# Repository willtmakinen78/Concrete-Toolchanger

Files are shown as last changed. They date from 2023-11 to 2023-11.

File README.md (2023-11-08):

# Concrete-Toolchanger
My senior thesis project from Princeton consisted of developing a multi-material concrete 3D-printer.

Using an E3D TOolchanger as the base motion system, custom concrete and silicone extruders were developed to be compatible with the toolchanging system.
A system for reliably priming the polymer Hemera extruders was also developed. The mechanics and electronics were controlled using a Duet board and RRF3,
which allowed for all of the toolchanging procedures and material interactions to be controlled by macros. Additionally, rather than using a traditional
slicer, FullControlGCode was used to create parametric toolpaths tailored to each type of extruder. Together, silicone and polymers were combined with
cement and mortar to create new concrete multi-materials with augmented material properties.

Check out the full thesis PDF for more details!

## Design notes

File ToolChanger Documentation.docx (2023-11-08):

ToolChanger Documentation

Introduction

Rather than being a full step-by-step guide, this document is mainly designed to serve as a collection of information sources with brief explanations in between. The other information sources linked here explain the various parts of the system well and in more detail than could be provided here, so they should be the primary resources for troubleshooting with this document only filling in the gaps.

Connecting to the ToolChanger

The printer can be accessed in two ways, over USB (https://learn.ooznest.co.uk/Guide/1.+Connecting+your+Duet+via+USB+-+Windows/123) and via the Duet Web Control (https://duet3d.dozuki.com/c/DuetWebControl) interface. The USB interface is minimal, and should only be used when first connecting the Duet control board (the Duet 2 Ethernet (https://docs.duet3d.com/Duet3D_hardware/Duet_2_family/Duet_2_WiFi_Ethernet_Hardware_Overview) is currently being used) to a network. The Duet board was configured over USB to use the static IP address (https://docs.duet3d.com/Duet3D_hardware/Duet_2_family/Duet_2_WiFi_Ethernet_Hardware_Overview) of 192.168.2.1. Then, the ethernet cable was plugged directly into an ethernet port of the control computer, and configured as is described here (https://duet3d.dozuki.com/Wiki/Setting_up_networking_on_Duet#Section_Wired_direct_connection). With this, the Duet Web Control interface can be accessed by going to 192.168.2.1 in a web browser.

Using Duet Web Control

An overview of the various functions of Duet Web Control is available here (https://duet3d.dozuki.com/Wiki/Duet_Web_Control_v2_and_v3_%28DWC%29_Manual). The most important aspects of it specific to the ToolChanger are the macro files (https://duet3d.dozuki.com/Wiki/Setting_up_macro_files_for_common_tasks) accessible from the Macros tab and system .g gcode files accessible from the System tab. The macro file do not have a file extension and can only be run from the Marcos or Dashboard tabs. The gcode files in the System tab have the .g file extension and can be run from anywhere using the M98 (https://duet3d.dozuki.com/Wiki/M98) command. This can be from the built-in console, within toolpath gcode files, or even from within other system .g files.

The most important system file is config.g. This is run at system startup and whenever the printer is reset, and sets the configuration of toolheads, heaters, offsets, and more. Looking through it, most of the lines are commented describing what is being configured, and each M command can be googled to get more information on what they are doing. Most relevant to the work being done this summer is lines 127-136 configuring the toolhead offsets. These will need to be modified if the geometry of any of the toolheads are changed, putting their nozzles in different locations.

There are also various system .g files used internally by the firmware of the printer, as described here (https://duet3d.dozuki.com/Wiki/ConfiguringRepRapFirmwareCartesianPrinter). These are used during various actions such as pausing, resuming, and stopping a print. The files that will most likely need to be changed are the tpre[tool number], tpost[tool number] and tfree[tool number]. These are called before and after a tool is selected (tpre and tpost) using the command T[toolnum] and when a tool is dropped off using T-1 (or when directly switching from one tool to another, e.g. if T0 is selected, sending the command T2 will actually execute T-1 and then T2. So the sequence of .g files called will be tfree0.g, tpre2.g, tpost2.g.). Opening up and reading these files, the tool pickup and drop-off locations in the tpre and tfree files will have to be changed if the tool geometries are changed, as well as the Z safety distances denoted by the WARNING comments. This is all described in more detail here (https://duet3d.dozuki.com/Wiki/Multiple_tools_and_Tool_change_macros#Section_Tool_Change_Macros).

Printer configuration

Currently, there are two plastic Hemera (https://e3d-online.com/products/e3d-hemera-direct-kit-1-75mm) tools, one syringe-based tool, and one hardware store silicone tube-based tool installed on the ToolChanger. The hemera tools both have 1.2mm nozzles installed, however smaller nozzles are on hand in the cardboard parts bin in the corner of the work bench. Additionally, two other complete hemera kits are also on hand, if one wishes to switch out the other two tools for additional plastic extruders.

From left to right, the tools are T0, T1, T2, and T3 which are hemera, hemera, syringe, and silicone tube extruders.

If a tool geometry were to be changed, it would have to be able to accept a tool plate (the metal part) and the plastic tool receptable (black plastic) in order for the kinematic coupling mechanism to be able to interface with it and for it to be able to be parked to the machine frame. The ToolChanger Github is available here (https://github.com/e3donline/ToolChanger) with PDFs and the original CAD parts.

Gcode/Toolpath Generation

The ToolChanger runs on RepRapFirmware3 (https://duet3d.dozuki.com/Wiki/RepRapFirmware_3_overview) (RRF3). Here (https://duet3d.dozuki.com/Wiki/Gcode) is its gcode dictionary. A notable feature is its scripting abilities (https://duet3d.dozuki.com/Wiki/GCode_Meta_Commands), which can be very powerful. Gcodes can be generated using slicers, grasshopper, or the excel-based FullControl Gcode (https://fullcontrolgcode.com/). FullControl was used extensively this past year to decent results. Example designs can be found in the FullControl folder in the IP Accelerator Dropbox. Note that if a different designer is used, the starting and ending gcodes from the FullControl designs should be copied over to ensure proper starting and ending of prints.

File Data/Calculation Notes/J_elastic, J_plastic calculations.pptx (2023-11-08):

## J_elastic, J_plastic calculations

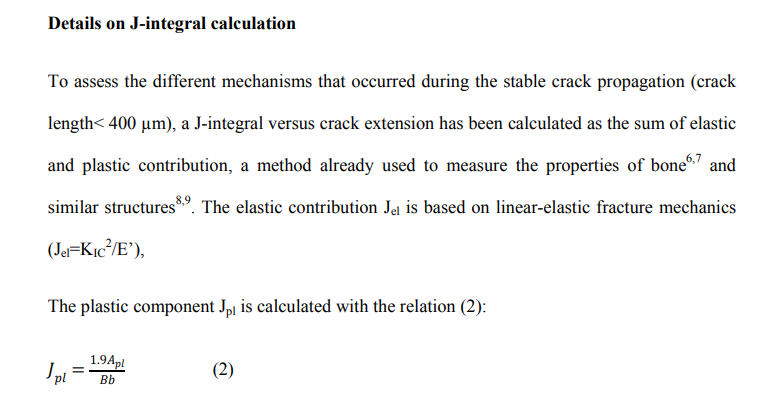
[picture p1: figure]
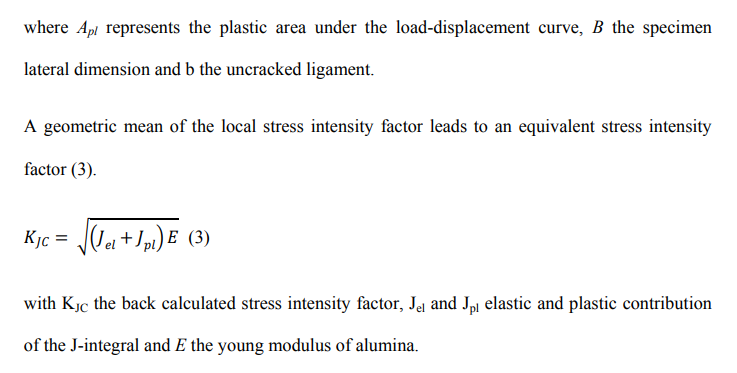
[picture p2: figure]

## J_elastic, J_plastic calculations

Term Definitions:
K = stress intensity factor is used to predict the stress state near the tip of a crack due to remote/residual stresses
Kc = critical stress intensity factor is the stress at which unstable crack propagation occurs
G = energy release rate, ie. rate at which energy is transformed as a material undergoes fracture
J = integral used to calculate the strain energy release rate per unit of fracture surface area
R-curve = quantification of the principle of increasing fracture resistance, as a function of crack length

## J_elastic, J_plastic calculations

Following E1820:
For basic test method using a notched 3PB test,
Where J_plastic is defined as:

## J_elastic, J_plastic calculations

For calculating J_elastic, we first need K:

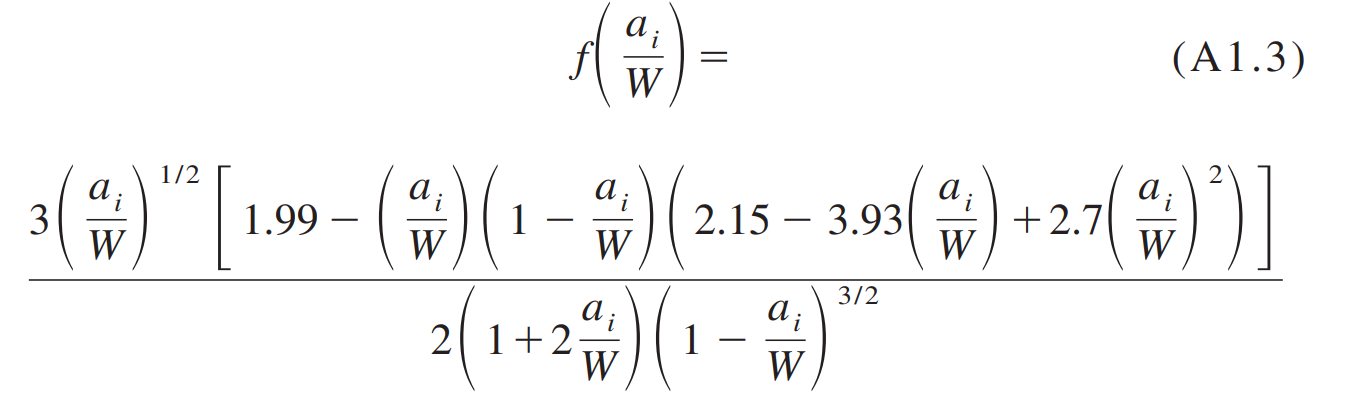
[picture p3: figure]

## J_elastic, J_plastic calculations

- P_i = force applied (N)
- S = span length (m)
- B = specimen thickness (m)
- B_N = specimen thickness between roots of the side grooves (m) – equivalent to B for our test (E399-20a 8.2.1)
- a_i = crack size (m)
- W = specimen depth (m)

## J_elastic, J_plastic calculations

Crack size, a_i, is calculated based on the CMOD measurements shown in the formulas in E399:

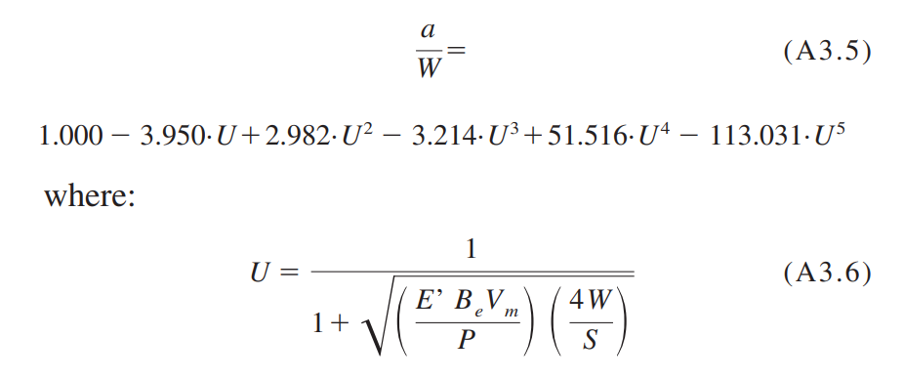
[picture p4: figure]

## J_elastic, J_plastic calculations

For J_plastic, we need the following terms:
…And alpha_0 = initial crack length

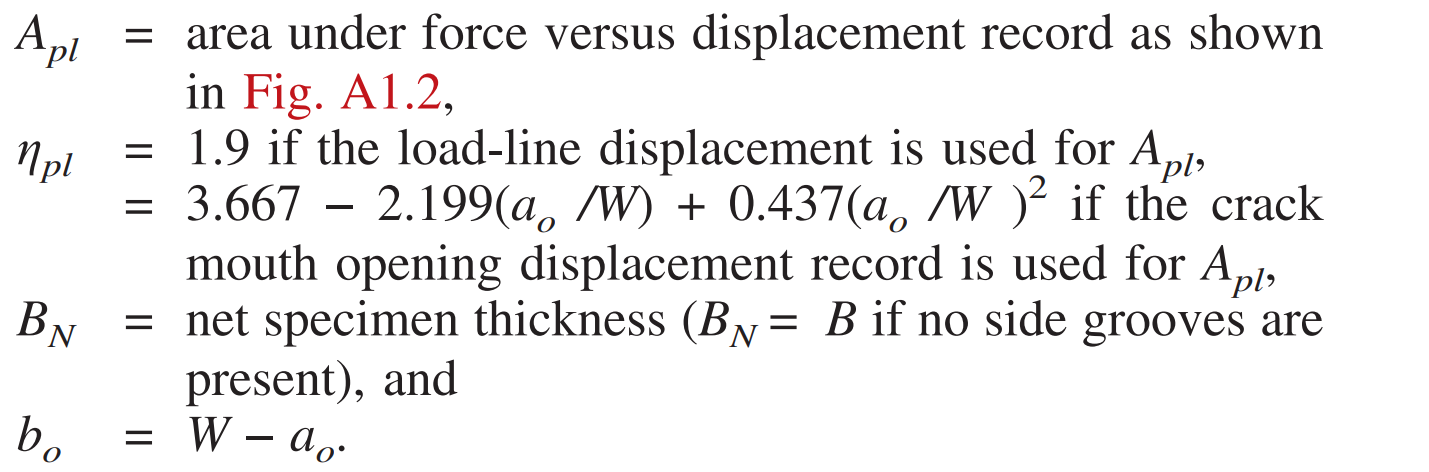
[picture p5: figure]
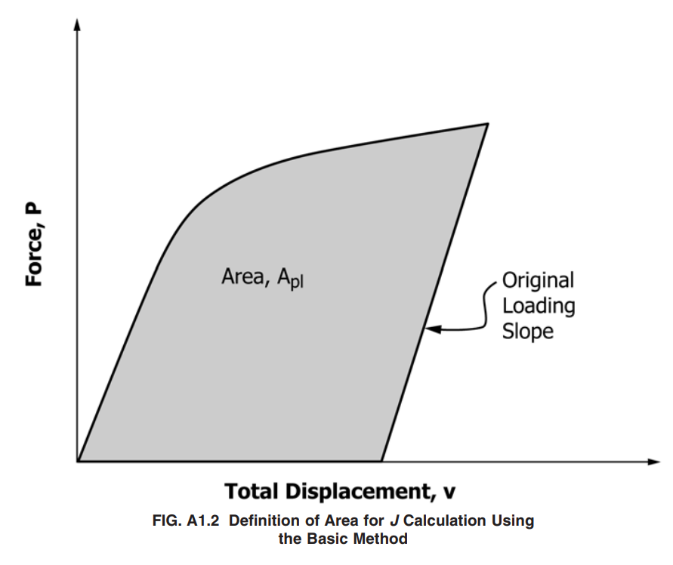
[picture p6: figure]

## J_elastic, J_plastic calculations

We can then solve for the final J value:
A correction factor is applied to the final J-integral

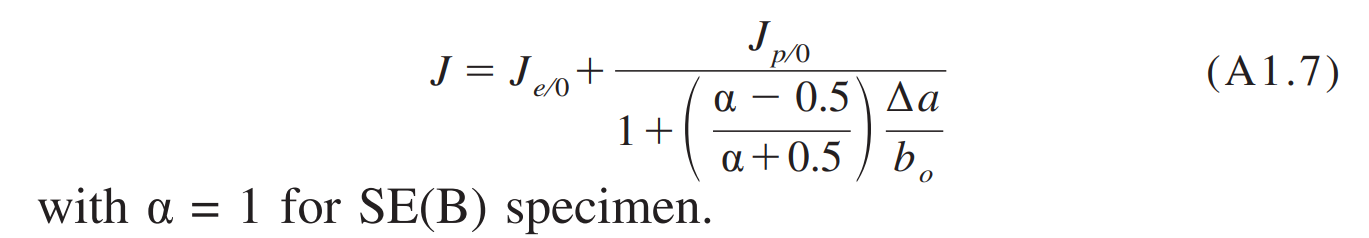
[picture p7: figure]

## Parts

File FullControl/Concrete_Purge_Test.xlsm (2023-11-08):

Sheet: Main Sheet
 |  |  |  |  |  |  |  | ;GCODE generated with FullControl GCODE Designer software - contact Andy Gleadall (a.gleadall@lboro.ac.uk) for more information
 |  |  |  |  |  |  |  |  |  |  |  |  |  | Recycle bin designs: | 1
Design ID: | Interlaced_Lines | Save to sheet: | MyDesigns
Feature |  |  |  |  |  |  |  |  |  |  |  | Comments
1 | Line | Cartesian | 227 | 163.6 | 0 | R-125 | R0 | R0 | Print | 1.6002 | 1.8 |  | Settings
2 | Line | Cartesian | R0 | R0 | R0 | R0 | R-2 | R0 | Print | 1.6002 | 1.8 |  | Zoffset | 1.3 | mm
3 | Line | Cartesian | R0 | R0 | R0 | R125 | R0 | R0 | Print | 1.6002 | 1.8 |  | FirstLayerExtrusionMultiplier | 1 | no units
4 | Line | Cartesian | R0 | R0 | R0 | R0 | R-4.7 | R0 | Print | 1.6002 | 1.8 |  | FirstLayerNozzleSpeedMultiplier | 1 | no units
5 | Cartesian repeat | 1-4 | 0 | -6.7 | 0 | 5 |  |  |  |  |  |  | ToolChange ID | Default |  | Default | Default | Default | Default | Default | Default | Raise3D_2nozzle | Tool changer | Default | Default | Default | Default | Default
6 | Retraction | 0 | 0 | 1.3 | 10000 |  |  |  |  |  |  |  | Start tool (after StartGCODE) | 0
7 | Line | Cartesian | R0 | R0 | R0 | R0 | R4.7 | R0 | Print | 1.6002 | 1.8
8 | Line | Cartesian | R0 | R0 | R0 | R-125 | R0 | R0 | Print | 1.6002 | 1.8 |  | BedTemp | 0 | C | 60 | 60 | 60 | 60 | 60 | 60 | 60 | 60 | 60 | 60 | 60 | 60 | 60
9 | Line | Cartesian | R0 | R0 | R0 | R0 | R2 | R0 | Print | 1.6002 | 1.8 |  | NozzleFeedratePrinting | 600 | mm/min
10 | Line | Cartesian | R0 | R0 | R0 | R125 | R0 | R0 | Print | 1.6002 | 1.8 |  | NozzleFeedrateTravelling | 3000 | mm/min
11 | Cartesian repeat | 7-10 | 0 | 6.7 | 0 | 5 |  |  |  |  |  |  | NozzleTemp | 0 | C | 210 | 210 | 210 | 215 | 220 | 210 | 210 | 210 | 210 | 210 | 210 | 210 | 210
12 | Retraction | 0 | 0 | 1.3 | 10000 |  |  |  |  |  |  |  | FeedstockFilamentDiameter | 40 | mm | 2.85 | 1.75 | 1.75 | 1.75 | 1.75 | 1.75 | 1.75 | 1.75 | 1.75 | 1.75 | 1.75 | 2.85 | 1.75
13 | Cartesian repeat | 1-12 | 0 | 0 | 2.6 | 1 |  |  |  |  |  |  | ExtrusionUnits | mm | mm OR mm3 | mm3 | mm | mm | mm | mm | mm | mm | mm | mm | mm | mm | mm3 | mm
14 |  |  |  |  |  |  |  |  |  |  |  |  | StartGCODE ID | Toolchanger |  | ULTI2+_Temps&Fan | Ender 3 | CR-10 | PrusaMini | AnycubicMegaS | Raise3D_1nozzle | Raise3D_2nozzle | ToolChanger_T0T2 | Snapmaker 2_A350 | REPRAP X400 | Voxel8 | Ultimaker3 | Artillery Genius
15 |  |  |  |  |  |  |  |  |  |  |  |  | EndGCODE ID | Toolchanger |  | ULTI2+_1 | Ender 3 | CR-10 | PrusaMini | AnycubicMegaS | Raise3D_1nozzle | Raise3D_2nozzle | ToolChanger_T0T2 | Snapmaker 2_A350 | REPRAP X400 | Voxel8 | Ultimaker3 | Artillery Genius
16 |  |  |  |  |  |  |  |  |  |  |  |  | Start X (after StartGCODE) | 200 | mm
17 |  |  |  |  |  |  |  |  |  |  |  |  | Start Y (after StartGCODE) | 75 | mm
18 |  |  |  |  |  |  |  |  |  |  |  |  | Start Z (after StartGCODE) | 0.3 | mm
19 |  |  |  |  |  |  |  |  |  |  |  |  | FanSpeed | 0
20 |  |  |  |  |  |  |  |  |  |  |  |  | AutoTravelRetraction? | no | yes/no
21 |  |  |  |  |  |  |  |  |  |  |  |  | - Threshold distance | 2 | mm
22 |  |  |  |  |  |  |  |  |  |  |  |  | - Retraction (E-value) | 1.25 | mm OR mm3
23 |  |  |  |  |  |  |  |  |  |  |  |  | - Retraction speed (F-value) | 2500 | mm/min
24 |  |  |  |  |  |  |  |  |  |  |  |  | - Unretraction (E-value) | 0 | mm OR mm3
25 |  |  |  |  |  |  |  |  |  |  |  |  | - Unretraction speed (F-value) | 2500 | mm/min
26 |  |  |  |  |  |  |  |  |  |  |  |  | - Z-hop | 0.65 | mm
27 |  |  |  |  |  |  |  |  |  |  |  |  | - Z-hop speed (F-value) | 10000 | mm/min
28
29 |  |  |  |  |  |  |  |  |  |  |  |  | Parameter name | Parameter value | Units
30 |  |  |  |  |  |  |  |  |  |  |  |  | ExtrusionSpacing | 2
31 |  |  |  |  |  |  |  |  |  |  |  |  | PolymerSpacing | 1.35
32 |  |  |  |  |  |  |  |  |  |  |  |  | ExtrusionWidth | 1.6002 |  | Stock: 3.75 | Dark green luer: 1.524 | Light green Luer: 1.6002
33 |  |  |  |  |  |  |  |  |  |  |  |  | ExtrusionHeight | 1.8
34 |  |  |  |  |  |  |  |  |  |  |  |  | StartTool | T2
35 |  |  |  |  |  |  |  |  |  |  |  |  | LayerHeight | 1.3
36 |  |  |  |  |  |  |  |  |  |  |  |  | Length | 125
37 |  |  |  |  |  |  |  |  |  |  |  |  | Width | 40
38 |  |  |  |  |  |  |  |  |  |  |  |  | Height | 10
39 |  |  |  |  |  |  |  |  |  |  |  |  | StartX | 100
40 |  |  |  |  |  |  |  |  |  |  |  |  | StartY | 125
 |  |  |  |  |  |  |  |  |  |  |  |  | RibRepeats | 5

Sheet: MyDesigns
Design ID: | Toolchanger_Template | Save to sheet: | MyDesigns |  |  |  |  |  |  |  |  |  |  |  |  |  |  |  |  |  |  |  |  |  |  |  |  |  |  | Save data (DO NOT DELETE): | Save time: 10/29/2021 2:03:18 PM | Design ID: | MyFirstDesign_v01 | Save to sheet: | MyDesigns
Feature |  |  |  |  |  |  |  |  |  |  |  |  | Comments
1 | Select a cell in this row and click the "Add Feature" button to begin your design |  |  |  |  |  |  |  |  |  |  |  |  | Settings
2 |  |  |  |  |  |  |  |  |  |  |  |  |  | Zoffset | 0.55 | mm
3 | See tutorials for information about how to use FullControl (www.fullcontrolgcode.com/tutorials) |  |  |  |  |  |  |  |  |  |  |  |  | FirstLayerExtrusionMultiplier | 0.83 | no units
4 |  |  |  |  |  |  |  |  |  |  |  |  |  | FirstLayerNozzleSpeedMultiplier | 0.5 | no units
5 |  |  |  |  |  |  |  |  |  |  |  |  |  | ToolChange ID | Default |  | Default | Default | Default | Default | Default | Default | Raise3D_2nozzle | Tool changer | Default | Default | Default | Default | Default
6 |  |  |  |  |  |  |  |  |  |  |  |  |  | Start tool (after StartGCODE) | 0
7
8 |  |  |  |  |  |  |  |  |  |  |  |  |  | BedTemp | 65 | C | 60 | 60 | 60 | 60 | 60 | 60 | 60 | 60 | 60 | 60 | 60 | 60 | 60
9 |  |  |  |  |  |  |  |  |  |  |  |  |  | NozzleFeedratePrinting | 1500 | mm/min
10 |  |  |  |  |  |  |  |  |  |  |  |  |  | NozzleFeedrateTravelling | 48000 | mm/min
11 |  |  |  |  |  |  |  |  |  |  |  |  |  | NozzleTemp | 220 | C | 210 | 210 | 210 | 215 | 220 | 210 | 210 | 210 | 210 | 210 | 210 | 210 | 210
12 |  |  |  |  |  |  |  |  |  |  |  |  |  | FeedstockFilamentDiameter | 1.75 | mm | 2.85 | 1.75 | 1.75 | 1.75 | 1.75 | 1.75 | 1.75 | 1.75 | 1.75 | 1.75 | 1.75 | 2.85 | 1.75
13 |  |  |  |  |  |  |  |  |  |  |  |  |  | ExtrusionUnits | 33 | mm OR mm3 | mm3 | mm | mm | mm | mm | mm | mm | mm | mm | mm | mm | mm3 | mm
14 |  |  |  |  |  |  |  |  |  |  |  |  |  | StartGCODE ID | Toolchanger |  | ULTI2+_Temps&Fan | Ender 3 | CR-10 | PrusaMini | AnycubicMegaS | Raise3D_1nozzle | Raise3D_2nozzle | ToolChanger_T0T2 | Snapmaker 2_A350 | REPRAP X400 | Voxel8 | Ultimaker3 | Artillery Genius
15 |  |  |  |  |  |  |  |  |  |  |  |  |  | EndGCODE ID | Toolchanger |  | ULTI2+_1 | Ender 3 | CR-10 | PrusaMini | AnycubicMegaS | Raise3D_1nozzle | Raise3D_2nozzle | ToolChanger_T0T2 | Snapmaker 2_A350 | REPRAP X400 | Voxel8 | Ultimaker3 | Artillery Genius
 |  |  |  |  |  |  |  |  |  |  |  |  |  | Start X (after StartGCODE) | 20 | mm
 |  |  |  |  |  |  |  |  |  |  |  |  |  | Start Y (after StartGCODE) | 10 | mm
 |  |  |  |  |  |  |  |  |  |  |  |  |  | Start Z (after StartGCODE) | 0.3 | mm
 |  |  |  |  |  |  |  |  |  |  |  |  |  | FanSpeed | 185
 |  |  |  |  |  |  |  |  |  |  |  |  |  | AutoTravelRetraction? | no | yes/no
 |  |  |  |  |  |  |  |  |  |  |  |  |  | - Threshold distance | 2 | mm
 |  |  |  |  |  |  |  |  |  |  |  |  |  | - Retraction (E-value) | 1.25 | mm OR mm3
 |  |  |  |  |  |  |  |  |  |  |  |  |  | - Retraction speed (F-value) | 2500 | mm/min
 |  |  |  |  |  |  |  |  |  |  |  |  |  | - Unretraction (E-value) | 0 | mm OR mm3
 |  |  |  |  |  |  |  |  |  |  |  |  |  | - Unretraction speed (F-value) | 2500 | mm/min
 |  |  |  |  |  |  |  |  |  |  |  |  |  | - Z-hop | 0.65 | mm
 |  |  |  |  |  |  |  |  |  |  |  |  |  | - Z-hop speed (F-value) | 10000 | mm/min
 |  |  |  |  |  |  |  |  |  |  |  |  |  | Parameter name | Parameter value | Units
Design ID: | Interlaced_Lines_1 | Save to sheet: | MyDesigns |  |  |  |  |  |  |  |  |  |  |  |  |  |  |  |  |  |  |  |  |  |  |  |  |  |  | Save data (DO NOT DELETE): | Save time: 11/16/2021 12:36:47 AM | Design ID: | Interlaced_Lines_1 | Save to sheet: | MyDesigns
Feature |  |  |  |  |  |  |  |  |  |  |  |  | Comments
1 | SKIP_Line | Cartesian | X1 | Y1 | Z1 | X2 | Y2 | Z2 | "Print" or "Travel" | NomWidth | NomHeight | E=?;F=?;T=? EvalueOverride;F-SpeedOverride:ToolNumber |  | Settings
2 | SKIP_Custom GCODE | T | 0 |  |  |  |  |  |  |  |  |  | first layer | Zoffset | 0.55 | mm
3 | SKIP_Line | Cartesian | R0 | R0 | R0 | 50 | 50 | 0.55 | Travel |  |  |  |  | FirstLayerExtrusionMultiplier | 0.83 | no units
4 | Line | Cartesian | 100 | 125 | 0 | #NAME? | R0 | R0 | Print | 1.6002 | 1.8 |  |  | FirstLayerNozzleSpeedMultiplier | 0.85 | no units
5 | Line | Cartesian | R0 | R0 | R0 | R0 | R125 | R0 | Print | 1.6002 | 1.8 |  |  | ToolChange ID | Default |  | Default | Default | Default | Default | Default | Default | Raise3D_2nozzle | Tool changer | Default | Default | Default | Default | Default
6 | Line | Cartesian | R0 | R0 | R0 | #NAME? | R0 | R0 | Print | 1.6002 | 1.8 |  |  | Start tool (after StartGCODE) | 0
7 | Line | Cartesian | R0 | R0 | R0 | R0 | R-125 | R0 | Print | 1.6002 | 1.8
8 | Cartesian repeat | 4-7 | #NAME? | 0 | 0 | 20 |  |  |  |  |  |  |  | BedTemp | 65 | C | 60 | 60 | 60 | 60 | 60 | 60 | 60 | 60 | 60 | 60 | 60 | 60 | 60
9 | Custom GCODE | M98 P"parkprep.g" |  |  |  |  |  |  |  |  |  |  |  | NozzleFeedratePrinting | 1500 | mm/min
10 | Custom GCODE | T | 1 |  |  |  |  |  |  |  |  |  |  | NozzleFeedrateTravelling | 48000 | mm/min
11 | Custom GCODE | M98 P"prime.g" |  |  |  |  |  |  |  |  |  |  |  | NozzleTemp | 220 | C | 210 | 210 | 210 | 215 | 220 | 210 | 210 | 210 | 210 | 210 | 210 | 210 | 210
12 | SKIP_Line | Cartesian | R0 | R0 | R0 | #NAME? | #NAME? | 0.55 | Travel |  |  |  |  | FeedstockFilamentDiameter | 1.75 | mm | 2.85 | 1.75 | 1.75 | 1.75 | 1.75 | 1.75 | 1.75 | 1.75 | 1.75 | 1.75 | 1.75 | 2.85 | 1.75
13 | Line | Cartesian | #NAME? | #NAME? | 0.0001 | R0 | R-125 | R0 | Print | 1.6002 | 1.8 |  |  | ExtrusionUnits | 33 | mm OR mm3 | mm3 | mm | mm | mm | mm | mm | mm | mm | mm | mm | mm | mm3 | mm
14 | Line | Cartesian | R0 | R0 | R0 | #NAME? | R0 | R0 | Print | 1.6002 | 1.8 |  |  | StartGCODE ID | Toolchanger |  | ULTI2+_Temps&Fan | Ender 3 | CR-10 | PrusaMini | AnycubicMegaS | Raise3D_1nozzle | Raise3D_2nozzle | ToolChanger_T0T2 | Snapmaker 2_A350 | REPRAP X400 | Voxel8 | Ultimaker3 | Artillery Genius
15 | Line | Cartesian | R0 | R0 | R0 | R0 | R125 | R0 | Print | 1.6002 | 1.8 |  |  | EndGCODE ID | Toolchanger |  | ULTI2+_1 | Ender 3 | CR-10 | PrusaMini | AnycubicMegaS | Raise3D_1nozzle | Raise3D_2nozzle | ToolChanger_T0T2 | Snapmaker 2_A350 | REPRAP X400 | Voxel8 | Ultimaker3 | Artillery Genius
16 | Line | Cartesian | R0 | R0 | R0 | #NAME? | R0 | R0 | Print | 1.6002 | 1.8 |  |  | Start X (after StartGCODE) | 20 | mm
17 | Cartesian repeat | 13-16 | #NAME? | 0 | 0 | 20 |  |  |  |  |  |  |  | Start Y (after StartGCODE) | 10 | mm
18 | Retraction | 1.25 | 2100 | 1.3 | 10000 |  |  |  |  |  |  |  |  | Start Z (after StartGCODE) | 0.3 | mm
19 | SKIP_Line | Cartesian | R0 | R0 | R0 | #NAME? | #NAME? |  | Travel |  |  |  |  | FanSpeed | 0
20 | Line | Cartesian | #NAME? | #NAME? | R0 | R0 | R-125 | R0 | Print | 1.6002 | 1.8 |  |  | AutoTravelRetraction? | no | yes/no
21 | Line | Cartesian | R0 | R0 | R0 | #NAME? | R0 | R0 | Print | 1.6002 | 1.8 |  |  | - Threshold distance | 2 | mm
22 | Line | Cartesian | R0 | R0 | R0 | R0 | R125 | R0 | Print | 1.6002 | 1.8 |  |  | - Retraction (E-value) | 1.25 | mm OR mm3
23 | Line | Cartesian | R0 | R0 | R0 | #NAME? | R0 | R0 | Print | 1.6002 | 1.8 |  |  | - Retraction speed (F-value) | 2500 | mm/min
24 | Cartesian repeat | 20-23 | #NAME? | 0 | 0 | 20 |  |  |  |  |  |  |  | - Unretraction (E-value) | 0 | mm OR mm3
25 | Custom GCODE | M98 P"parkprep.g" |  |  |  |  |  |  |  |  |  |  |  | - Unretraction speed (F-value) | 2500 | mm/min
26 | Custom GCODE | T | 0 |  |  |  |  |  |  |  |  |  |  | - Z-hop | 0.65 | mm
27 | Custom GCODE | M98 P"prime.g" |  |  |  |  |  |  |  |  |  |  |  | - Z-hop speed (F-value) | 10000 | mm/min
28 | SKIP_Line | Cartesian | R0 | R0 | R0 | 50 | 50 | 1.3 | Travel
29 | Line | Cartesian | 100 | 125 | 1.3 | #NAME? | R0 | R0 | Print | 1.6002 | 1.8 |  |  | Parameter name | Parameter value | Units
30 | Line | Cartesian | R0 | R0 | R0 | R0 | R125 | R0 | Print | 1.6002 | 1.8 |  |  | ExtrusionSpacing_L1 | 1.35
31 | Line | Cartesian | R0 | R0 | R0 | #NAME? | R0 | R0 | Print | 1.6002 | 1.8 |  |  | ExtrusionSpacing | 1.1
32 | Line | Cartesian | R0 | R0 | R0 | R0 | R-125 | R0 | Print | 1.6002 | 1.8 |  |  | ExtrusionWidth | 1.2
33 | Cartesian repeat | 29-32 | #NAME? | 0 | 0 | 20 |  |  |  |  |  |  |  | ExtrusionHeight | 0.9 |  |  |  |  |  |  |  |  |  |  |  |  |  |  | Save data (DO NOT DELETE): | Save time: 11/15/2021 8:33:46 PM | Design ID: | Interlaced_Lines_Alternating | Save to sheet: | MyDesigns
34 | Retraction | 1.25 | 2100 | 1.3 | 10000 |  |  |  |  |  |  |  |  | StartTool | T0
35 | Cartesian repeat | 8,9,10,11,17,18,24,25,26,27,33,34 | 0 | 0 | 2.6 | 20 |  |  |  |  |  |  |  | LayerHeight | 0.9
36 |  |  |  |  |  |  |  |  |  |  |  |  |  | Length | 50
37 |  |  |  |  |  |  |  |  |  |  |  |  |  | StartX | 50
38 |  |  |  |  |  |  |  |  |  |  |  |  |  | StartY | 75
39
40
Design ID: | Interlaced_Lines_Alternate_1 | Save to sheet: | MyDesigns |  |  |  |  |  |  |  |  |  |  |  |  |  |  |  |  |  |  |  |  |  |  |  |  |  |  | Save data (DO NOT DELETE): | Save time: 11/16/2021 12:42:00 AM | Design ID: | Interlaced_Lines_Alternate_1 | Save to sheet: | MyDesigns
Feature |  |  |  |  |  |  |  |  |  |  |  |  | Comments
1 | SKIP_Line | Cartesian | X1 | Y1 | Z1 | X2 | Y2 | Z2 | "Print" or "Travel" | NomWidth | NomHeight | E=?;F=?;T=? EvalueOverride;F-SpeedOverride:ToolNumber |  | Settings
2 | SKIP_Custom GCODE | T | 0 |  |  |  |  |  |  |  |  |  | first layer | Zoffset | 0.55 | mm
3 | SKIP_Line | Cartesian | R0 | R0 | R0 | 50 | 50 | 0.55 | Travel |  |  |  |  | FirstLayerExtrusionMultiplier | 0.83 | no units
4 | Line | Cartesian | 100 | 125 | 0 | #NAME? | R0 | R0 | Print | 1.6002 | 1.8 |  |  | FirstLayerNozzleSpeedMultiplier | 0.85 | no units
5 | Line | Cartesian | R0 | R0 | R0 | R0 | R125 | R0 | Print | 1.6002 | 1.8 |  |  | ToolChange ID | Default |  | Default | Default | Default | Default | Default | Default | Raise3D_2nozzle | Tool changer | Default | Default | Default | Default | Default
6 | Line | Cartesian | R0 | R0 | R0 | #NAME? | R0 | R0 | Print | 1.6002 | 1.8 |  |  | Start tool (after StartGCODE) | 0
7 | Line | Cartesian | R0 | R0 | R0 | R0 | R-125 | R0 | Print | 1.6002 | 1.8
8 | Cartesian repeat | 4-7 | #NAME? | 0 | 0 | 20 |  |  |  |  |  |  |  | BedTemp | 65 | C | 60 | 60 | 60 | 60 | 60 | 60 | 60 | 60 | 60 | 60 | 60 | 60 | 60
9 | Custom GCODE | M98 P"parkprep.g" |  |  |  |  |  |  |  |  |  |  |  | NozzleFeedratePrinting | 1500 | mm/min
10 | Custom GCODE | T | 1 |  |  |  |  |  |  |  |  |  |  | NozzleFeedrateTravelling | 48000 | mm/min
11 | Custom GCODE | M98 P"prime.g" |  |  |  |  |  |  |  |  |  |  |  | NozzleTemp | 220 | C | 210 | 210 | 210 | 215 | 220 | 210 | 210 | 210 | 210 | 210 | 210 | 210 | 210
12 | SKIP_Line | Cartesian | R0 | R0 | R0 | #NAME? | #NAME? | 0.55 | Travel |  |  |  |  | FeedstockFilamentDiameter | 1.75 | mm | 2.85 | 1.75 | 1.75 | 1.75 | 1.75 | 1.75 | 1.75 | 1.75 | 1.75 | 1.75 | 1.75 | 2.85 | 1.75
13 | Line | Cartesian | #NAME? | #NAME? | 0.0001 | R0 | R-125 | R0 | Print | 1.6002 | 1.8 |  |  | ExtrusionUnits | 33 | mm OR mm3 | mm3 | mm | mm | mm | mm | mm | mm | mm | mm | mm | mm | mm3 | mm
14 | Line | Cartesian | R0 | R0 | R0 | #NAME? | R0 | R0 | Print | 1.6002 | 1.8 |  |  | StartGCODE ID | Toolchanger |  | ULTI2+_Temps&Fan | Ender 3 | CR-10 | PrusaMini | AnycubicMegaS | Raise3D_1nozzle | Raise3D_2nozzle | ToolChanger_T0T2 | Snapmaker 2_A350 | REPRAP X400 | Voxel8 | Ultimaker3 | Artillery Genius
15 | Line | Cartesian | R0 | R0 | R0 | R0 | R125 | R0 | Print | 1.6002 | 1.8 |  |  | EndGCODE ID | Toolchanger |  | ULTI2+_1 | Ender 3 | CR-10 | PrusaMini | AnycubicMegaS | Raise3D_1nozzle | Raise3D_2nozzle | ToolChanger_T0T2 | Snapmaker 2_A350 | REPRAP X400 | Voxel8 | Ultimaker3 | Artillery Genius
16 | Line | Cartesian | R0 | R0 | R0 | #NAME? | R0 | R0 | Print | 1.6002 | 1.8 |  |  | Start X (after StartGCODE) | 20 | mm
17 | Cartesian repeat | 13-16 | #NAME? | 0 | 0 | 20 |  |  |  |  |  |  |  | Start Y (after StartGCODE) | 10 | mm
18 | Retraction | 1.25 | 2100 | 1.3 | 10000 |  |  |  |  |  |  |  |  | Start Z (after StartGCODE) | 0.3 | mm
19 | SKIP_Line | Cartesian | R0 | R0 | R0 | #NAME? | #NAME? |  | Travel |  |  |  |  | FanSpeed | 0
20 | Line | Cartesian | 100 | 125 | R0 | #NAME? | R0 | R0 | Print | 1.6002 | 1.8 |  |  | AutoTravelRetraction? | no | yes/no
21 | Line | Cartesian | R0 | R0 | R0 | R0 | R125 | R0 | Print | 1.6002 | 1.8 |  |  | - Threshold distance | 2 | mm
22 | Line | Cartesian | R0 | R0 | R0 | #NAME? | R0 | R0 | Print | 1.6002 | 1.8 |  |  | - Retraction (E-value) | 1.25 | mm OR mm3
23 | Line | Cartesian | R0 | R0 | R0 | R0 | R-125 | R0 | Print | 1.6002 | 1.8 |  |  | - Retraction speed (F-value) | 2500 | mm/min
24 | Cartesian repeat | 20-23 | #NAME? | 0 | 0 | 20 |  |  |  |  |  |  |  | - Unretraction (E-value) | 0 | mm OR mm3
25 | Custom GCODE | M98 P"parkprep.g" |  |  |  |  |  |  |  |  |  |  |  | - Unretraction speed (F-value) | 2500 | mm/min
26 | Custom GCODE | T | 0 |  |  |  |  |  |  |  |  |  |  | - Z-hop | 0.65 | mm
27 | Custom GCODE | M98 P"prime.g" |  |  |  |  |  |  |  |  |  |  |  | - Z-hop speed (F-value) | 10000 | mm/min
28 | SKIP_Line | Cartesian | R0 | R0 | R0 | 50 | 50 | 1.3 | Travel
29 | Line | Cartesian | #NAME? | #NAME? | 0.9 | R0 | R-125 | R0 | Print | 1.6002 | 1.8 |  |  | Parameter name | Parameter value | Units
30 | Line | Cartesian | R0 | R0 | R0 | #NAME? | R0 | R0 | Print | 1.6002 | 1.8 |  |  | ExtrusionSpacing_L1 | 1.35
31 | Line | Cartesian | R0 | R0 | R0 | R0 | R125 | R0 | Print | 1.6002 | 1.8 |  |  | ExtrusionSpacing | 1.1
32 | Line | Cartesian | R0 | R0 | R0 | #NAME? | R0 | R0 | Print | 1.6002 | 1.8 |  |  | ExtrusionWidth | 1.2
33 | Cartesian repeat | 29-32 | #NAME? | 0 | 0 | 20 |  |  |  |  |  |  |  | ExtrusionHeight | 0.9 |  |  |  |  |  |  |  |  |  |  |  |  |  |  | Save data (DO NOT DELETE): | Save time: 11/15/2021 8:42:35 PM | Design ID: | Interlaced_Lines | Save to sheet: | MyDesigns
34 | Retraction | 1.25 | 2100 | 1.3 | 10000 |  |  |  |  |  |  |  |  | StartTool | T0
35 | Cartesian repeat | 8,9,10,11,17,18,24,25,26,27,33,34 | 0 | 0 | 2.6 | 20 |  |  |  |  |  |  |  | LayerHeight | 0.9
36 |  |  |  |  |  |  |  |  |  |  |  |  |  | Length | 50
37 |  |  |  |  |  |  |  |  |  |  |  |  |  | StartX | 50
38 |  |  |  |  |  |  |  |  |  |  |  |  |  | StartY | 75
39
40
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

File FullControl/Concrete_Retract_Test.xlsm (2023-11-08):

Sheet: Main Sheet
 |  |  |  |  |  |  |  | ;GCODE generated with FullControl GCODE Designer software - contact Andy Gleadall (a.gleadall@lboro.ac.uk) for more information
 |  |  |  |  |  |  |  |  |  |  |  |  |  |  | Recycle bin designs: | 1
Design ID: | Interlaced_Lines | Save to sheet: | MyDesigns
Feature |  |  |  |  |  |  |  |  |  |  |  |  | Comments
1 | Line | Cartesian | R0 | R0 | R0 | 225 | 140 | 0 | Print | 3.75 | 2.8 |  |  | Settings
2 | Line | Cartesian | R0 | R0 | 0 | R0 | R-130 | 0 | Print | 3.75 | 2.8 |  |  | Zoffset | 2 | mm
3 | Line | Cartesian | R0 | R0 | R0 | R-5 | R0 | R0 | Print | 3.75 | 2.8 |  |  | FirstLayerExtrusionMultiplier | 1 | no units
4 | Line | Cartesian | R0 | R0 | R0 | R0 | R130 | 0 | Print | 3.75 | 2.8 |  |  | FirstLayerNozzleSpeedMultiplier | 1 | no units
5 | Retraction | 0 | 80 | 2 | 3000 |  |  |  |  |  |  |  |  | ToolChange ID | Default |  | Default | Default | Default | Default | Default | Default | Raise3D_2nozzle | Tool changer | Default | Default | Default | Default | Default
6 | Line | Cartesian | R0 | R0 | R0 | R-25 | R0 | 0 | Print | 3.75 | 2.8 |  |  | Start tool (after StartGCODE) | 0
7 | SKIP_Retraction | -0.45 | 80 | 0 | 0
8 | Line | Cartesian | R0 | R0 | R0 | R0 | R-130 | 0 | Print | 3.75 | 2.8 |  |  | BedTemp | 0 | C | 60 | 60 | 60 | 60 | 60 | 60 | 60 | 60 | 60 | 60 | 60 | 60 | 60
9 | SKIP_Retraction | 0.35 | 80 | 2 | 3000 |  |  |  |  |  |  |  |  | NozzleFeedratePrinting | 600 | mm/min
10 | Line | Cartesian | R0 | R0 | R0 | R0 | R130 | 0 | Print | 3.75 | 2.8 | T=1 |  | NozzleFeedrateTravelling | 3000 | mm/min
11 |  |  |  |  |  |  |  |  |  |  |  |  |  | NozzleTemp | 0 | C | 210 | 210 | 210 | 215 | 220 | 210 | 210 | 210 | 210 | 210 | 210 | 210 | 210
12 |  |  |  |  |  |  |  |  |  |  |  |  |  | FeedstockFilamentDiameter | 40 | mm | 2.85 | 1.75 | 1.75 | 1.75 | 1.75 | 1.75 | 1.75 | 1.75 | 1.75 | 1.75 | 1.75 | 2.85 | 1.75
13 |  |  |  |  |  |  |  |  |  |  |  |  |  | ExtrusionUnits | 33 | mm OR mm3 | mm3 | mm | mm | mm | mm | mm | mm | mm | mm | mm | mm | mm3 | mm
14 |  |  |  |  |  |  |  |  |  |  |  |  |  | StartGCODE ID | Toolchanger |  | ULTI2+_Temps&Fan | Ender 3 | CR-10 | PrusaMini | AnycubicMegaS | Raise3D_1nozzle | Raise3D_2nozzle | ToolChanger_T0T2 | Snapmaker 2_A350 | REPRAP X400 | Voxel8 | Ultimaker3 | Artillery Genius
15 |  |  |  |  |  |  |  |  |  |  |  |  |  | EndGCODE ID | Toolchanger |  | ULTI2+_1 | Ender 3 | CR-10 | PrusaMini | AnycubicMegaS | Raise3D_1nozzle | Raise3D_2nozzle | ToolChanger_T0T2 | Snapmaker 2_A350 | REPRAP X400 | Voxel8 | Ultimaker3 | Artillery Genius
16 |  |  |  |  |  |  |  |  |  |  |  |  |  | Start X (after StartGCODE) | 275 | mm
17 |  |  |  |  |  |  |  |  |  |  |  |  |  | Start Y (after StartGCODE) | 160 | mm
18 |  |  |  |  |  |  |  |  |  |  |  |  |  | Start Z (after StartGCODE) | 1.3 | mm
19 |  |  |  |  |  |  |  |  |  |  |  |  |  | FanSpeed | 0
20 |  |  |  |  |  |  |  |  |  |  |  |  |  | AutoTravelRetraction? | no | yes/no
21 |  |  |  |  |  |  |  |  |  |  |  |  |  | - Threshold distance | 2 | mm
22 |  |  |  |  |  |  |  |  |  |  |  |  |  | - Retraction (E-value) | 1.25 | mm OR mm3
23 |  |  |  |  |  |  |  |  |  |  |  |  |  | - Retraction speed (F-value) | 2500 | mm/min
24 |  |  |  |  |  |  |  |  |  |  |  |  |  | - Unretraction (E-value) | 0 | mm OR mm3
25 |  |  |  |  |  |  |  |  |  |  |  |  |  | - Unretraction speed (F-value) | 2500 | mm/min
26 |  |  |  |  |  |  |  |  |  |  |  |  |  | - Z-hop | 0.65 | mm
27 |  |  |  |  |  |  |  |  |  |  |  |  |  | - Z-hop speed (F-value) | 10000 | mm/min
28
29 |  |  |  |  |  |  |  |  |  |  |  |  |  | Parameter name | Parameter value | Units
30 |  |  |  |  |  |  |  |  |  |  |  |  |  | ExtrusionSpacing | 5 | 2
31
32 |  |  |  |  |  |  |  |  |  |  |  |  |  | ExtrusionWidth | 3.75 | 1.6002
33 |  |  |  |  |  |  |  |  |  |  |  |  |  | ExtrusionHeight | 2.8 | 1.8
34 |  |  |  |  |  |  |  |  |  |  |  |  |  | StartTool | T2
35 |  |  |  |  |  |  |  |  |  |  |  |  |  | LayerHeight | 2 | 1.3
36 |  |  |  |  |  |  |  |  |  |  |  |  |  | Length | 125
37 |  |  |  |  |  |  |  |  |  |  |  |  |  | Width | 25
38 |  |  |  |  |  |  |  |  |  |  |  |  |  | Height | 15.3
39 |  |  |  |  |  |  |  |  |  |  |  |  |  | StartX | 40
40 |  |  |  |  |  |  |  |  |  |  |  |  |  | StartY | 100

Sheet: MyDesigns
Design ID: | Toolchanger_Template | Save to sheet: | MyDesigns |  |  |  |  |  |  |  |  |  |  |  |  |  |  |  |  |  |  |  |  |  |  |  |  |  |  | Save data (DO NOT DELETE): | Save time: 10/29/2021 2:03:18 PM | Design ID: | MyFirstDesign_v01 | Save to sheet: | MyDesigns
Feature |  |  |  |  |  |  |  |  |  |  |  |  | Comments
1 | Select a cell in this row and click the "Add Feature" button to begin your design |  |  |  |  |  |  |  |  |  |  |  |  | Settings
2 |  |  |  |  |  |  |  |  |  |  |  |  |  | Zoffset | 0.55 | mm
3 | See tutorials for information about how to use FullControl (www.fullcontrolgcode.com/tutorials) |  |  |  |  |  |  |  |  |  |  |  |  | FirstLayerExtrusionMultiplier | 0.83 | no units
4 |  |  |  |  |  |  |  |  |  |  |  |  |  | FirstLayerNozzleSpeedMultiplier | 0.5 | no units
5 |  |  |  |  |  |  |  |  |  |  |  |  |  | ToolChange ID | Default |  | Default | Default | Default | Default | Default | Default | Raise3D_2nozzle | Tool changer | Default | Default | Default | Default | Default
6 |  |  |  |  |  |  |  |  |  |  |  |  |  | Start tool (after StartGCODE) | 0
7
8 |  |  |  |  |  |  |  |  |  |  |  |  |  | BedTemp | 65 | C | 60 | 60 | 60 | 60 | 60 | 60 | 60 | 60 | 60 | 60 | 60 | 60 | 60
9 |  |  |  |  |  |  |  |  |  |  |  |  |  | NozzleFeedratePrinting | 1500 | mm/min
10 |  |  |  |  |  |  |  |  |  |  |  |  |  | NozzleFeedrateTravelling | 48000 | mm/min
11 |  |  |  |  |  |  |  |  |  |  |  |  |  | NozzleTemp | 220 | C | 210 | 210 | 210 | 215 | 220 | 210 | 210 | 210 | 210 | 210 | 210 | 210 | 210
12 |  |  |  |  |  |  |  |  |  |  |  |  |  | FeedstockFilamentDiameter | 1.75 | mm | 2.85 | 1.75 | 1.75 | 1.75 | 1.75 | 1.75 | 1.75 | 1.75 | 1.75 | 1.75 | 1.75 | 2.85 | 1.75
13 |  |  |  |  |  |  |  |  |  |  |  |  |  | ExtrusionUnits | 33 | mm OR mm3 | mm3 | mm | mm | mm | mm | mm | mm | mm | mm | mm | mm | mm3 | mm
14 |  |  |  |  |  |  |  |  |  |  |  |  |  | StartGCODE ID | Toolchanger |  | ULTI2+_Temps&Fan | Ender 3 | CR-10 | PrusaMini | AnycubicMegaS | Raise3D_1nozzle | Raise3D_2nozzle | ToolChanger_T0T2 | Snapmaker 2_A350 | REPRAP X400 | Voxel8 | Ultimaker3 | Artillery Genius
15 |  |  |  |  |  |  |  |  |  |  |  |  |  | EndGCODE ID | Toolchanger |  | ULTI2+_1 | Ender 3 | CR-10 | PrusaMini | AnycubicMegaS | Raise3D_1nozzle | Raise3D_2nozzle | ToolChanger_T0T2 | Snapmaker 2_A350 | REPRAP X400 | Voxel8 | Ultimaker3 | Artillery Genius
 |  |  |  |  |  |  |  |  |  |  |  |  |  | Start X (after StartGCODE) | 20 | mm
 |  |  |  |  |  |  |  |  |  |  |  |  |  | Start Y (after StartGCODE) | 10 | mm
 |  |  |  |  |  |  |  |  |  |  |  |  |  | Start Z (after StartGCODE) | 0.3 | mm
 |  |  |  |  |  |  |  |  |  |  |  |  |  | FanSpeed | 185
 |  |  |  |  |  |  |  |  |  |  |  |  |  | AutoTravelRetraction? | no | yes/no
 |  |  |  |  |  |  |  |  |  |  |  |  |  | - Threshold distance | 2 | mm
 |  |  |  |  |  |  |  |  |  |  |  |  |  | - Retraction (E-value) | 1.25 | mm OR mm3
 |  |  |  |  |  |  |  |  |  |  |  |  |  | - Retraction speed (F-value) | 2500 | mm/min
 |  |  |  |  |  |  |  |  |  |  |  |  |  | - Unretraction (E-value) | 0 | mm OR mm3
 |  |  |  |  |  |  |  |  |  |  |  |  |  | - Unretraction speed (F-value) | 2500 | mm/min
 |  |  |  |  |  |  |  |  |  |  |  |  |  | - Z-hop | 0.65 | mm
 |  |  |  |  |  |  |  |  |  |  |  |  |  | - Z-hop speed (F-value) | 10000 | mm/min
 |  |  |  |  |  |  |  |  |  |  |  |  |  | Parameter name | Parameter value | Units
Design ID: | Interlaced_Lines_1 | Save to sheet: | MyDesigns |  |  |  |  |  |  |  |  |  |  |  |  |  |  |  |  |  |  |  |  |  |  |  |  |  |  | Save data (DO NOT DELETE): | Save time: 11/16/2021 12:36:47 AM | Design ID: | Interlaced_Lines_1 | Save to sheet: | MyDesigns
Feature |  |  |  |  |  |  |  |  |  |  |  |  | Comments
1 | SKIP_Line | Cartesian | X1 | Y1 | Z1 | X2 | Y2 | Z2 | "Print" or "Travel" | NomWidth | NomHeight | E=?;F=?;T=? EvalueOverride;F-SpeedOverride:ToolNumber |  | Settings
2 | SKIP_Custom GCODE | T | 0 |  |  |  |  |  |  |  |  |  | first layer | Zoffset | 0.55 | mm
3 | SKIP_Line | Cartesian | R0 | R0 | R0 | 50 | 50 | 0.55 | Travel |  |  |  |  | FirstLayerExtrusionMultiplier | 0.83 | no units
4 | Line | Cartesian | 40 | 100 | 0 | R15 | R0 | R0 | Print | 3.75 | 2.8 |  |  | FirstLayerNozzleSpeedMultiplier | 0.85 | no units
5 | Line | Cartesian | R0 | R0 | R0 | R0 | R125 | R0 | Print | 3.75 | 2.8 |  |  | ToolChange ID | Default |  | Default | Default | Default | Default | Default | Default | Raise3D_2nozzle | Tool changer | Default | Default | Default | Default | Default
6 | Line | Cartesian | R0 | R0 | R0 | R5 | R0 | R0 | Print | 3.75 | 2.8 |  |  | Start tool (after StartGCODE) | 0
7 | Line | Cartesian | R0 | R0 | R0 | R0 | R-125 | R0 | Print | 3.75 | 2.8
8 | Cartesian repeat | 4-7 | 20 | 0 | 0 | 20 |  |  |  |  |  |  |  | BedTemp | 65 | C | 60 | 60 | 60 | 60 | 60 | 60 | 60 | 60 | 60 | 60 | 60 | 60 | 60
9 | Custom GCODE | M98 P"parkprep.g" |  |  |  |  |  |  |  |  |  |  |  | NozzleFeedratePrinting | 1500 | mm/min
10 | Custom GCODE | T | 1 |  |  |  |  |  |  |  |  |  |  | NozzleFeedrateTravelling | 48000 | mm/min
11 | Custom GCODE | M98 P"prime.g" |  |  |  |  |  |  |  |  |  |  |  | NozzleTemp | 220 | C | 210 | 210 | 210 | 215 | 220 | 210 | 210 | 210 | 210 | 210 | 210 | 210 | 210
12 | SKIP_Line | Cartesian | R0 | R0 | R0 | 55 | 180 | 0.55 | Travel |  |  |  |  | FeedstockFilamentDiameter | 1.75 | mm | 2.85 | 1.75 | 1.75 | 1.75 | 1.75 | 1.75 | 1.75 | 1.75 | 1.75 | 1.75 | 1.75 | 2.85 | 1.75
13 | Line | Cartesian | 45 | 230 | 0.0001 | R0 | R-125 | R0 | Print | 3.75 | 2.8 |  |  | ExtrusionUnits | 33 | mm OR mm3 | mm3 | mm | mm | mm | mm | mm | mm | mm | mm | mm | mm | mm3 | mm
14 | Line | Cartesian | R0 | R0 | R0 | R5 | R0 | R0 | Print | 3.75 | 2.8 |  |  | StartGCODE ID | Toolchanger |  | ULTI2+_Temps&Fan | Ender 3 | CR-10 | PrusaMini | AnycubicMegaS | Raise3D_1nozzle | Raise3D_2nozzle | ToolChanger_T0T2 | Snapmaker 2_A350 | REPRAP X400 | Voxel8 | Ultimaker3 | Artillery Genius
15 | Line | Cartesian | R0 | R0 | R0 | R0 | R125 | R0 | Print | 3.75 | 2.8 |  |  | EndGCODE ID | Toolchanger |  | ULTI2+_1 | Ender 3 | CR-10 | PrusaMini | AnycubicMegaS | Raise3D_1nozzle | Raise3D_2nozzle | ToolChanger_T0T2 | Snapmaker 2_A350 | REPRAP X400 | Voxel8 | Ultimaker3 | Artillery Genius
16 | Line | Cartesian | R0 | R0 | R0 | R15 | R0 | R0 | Print | 3.75 | 2.8 |  |  | Start X (after StartGCODE) | 20 | mm
17 | Cartesian repeat | 13-16 | 20 | 0 | 0 | 20 |  |  |  |  |  |  |  | Start Y (after StartGCODE) | 10 | mm
18 | Retraction | 1.25 | 2100 | 2 | 10000 |  |  |  |  |  |  |  |  | Start Z (after StartGCODE) | 0.3 | mm
19 | SKIP_Line | Cartesian | R0 | R0 | R0 | 55 | 180 |  | Travel |  |  |  |  | FanSpeed | 0
20 | Line | Cartesian | 45 | 230 | R0 | R0 | R-125 | R0 | Print | 3.75 | 2.8 |  |  | AutoTravelRetraction? | no | yes/no
21 | Line | Cartesian | R0 | R0 | R0 | R5 | R0 | R0 | Print | 3.75 | 2.8 |  |  | - Threshold distance | 2 | mm
22 | Line | Cartesian | R0 | R0 | R0 | R0 | R125 | R0 | Print | 3.75 | 2.8 |  |  | - Retraction (E-value) | 1.25 | mm OR mm3
23 | Line | Cartesian | R0 | R0 | R0 | R15 | R0 | R0 | Print | 3.75 | 2.8 |  |  | - Retraction speed (F-value) | 2500 | mm/min
24 | Cartesian repeat | 20-23 | 20 | 0 | 0 | 20 |  |  |  |  |  |  |  | - Unretraction (E-value) | 0 | mm OR mm3
25 | Custom GCODE | M98 P"parkprep.g" |  |  |  |  |  |  |  |  |  |  |  | - Unretraction speed (F-value) | 2500 | mm/min
26 | Custom GCODE | T | 0 |  |  |  |  |  |  |  |  |  |  | - Z-hop | 0.65 | mm
27 | Custom GCODE | M98 P"prime.g" |  |  |  |  |  |  |  |  |  |  |  | - Z-hop speed (F-value) | 10000 | mm/min
28 | SKIP_Line | Cartesian | R0 | R0 | R0 | 50 | 50 | 2 | Travel
29 | Line | Cartesian | 40 | 100 | 2 | R15 | R0 | R0 | Print | 3.75 | 2.8 |  |  | Parameter name | Parameter value | Units
30 | Line | Cartesian | R0 | R0 | R0 | R0 | R125 | R0 | Print | 3.75 | 2.8 |  |  | ExtrusionSpacing_L1 | 1.35
31 | Line | Cartesian | R0 | R0 | R0 | R5 | R0 | R0 | Print | 3.75 | 2.8 |  |  | ExtrusionSpacing | 1.1
32 | Line | Cartesian | R0 | R0 | R0 | R0 | R-125 | R0 | Print | 3.75 | 2.8 |  |  | ExtrusionWidth | 1.2
33 | Cartesian repeat | 29-32 | 20 | 0 | 0 | 20 |  |  |  |  |  |  |  | ExtrusionHeight | 0.9 |  |  |  |  |  |  |  |  |  |  |  |  |  |  | Save data (DO NOT DELETE): | Save time: 11/15/2021 8:33:46 PM | Design ID: | Interlaced_Lines_Alternating | Save to sheet: | MyDesigns
34 | Retraction | 1.25 | 2100 | 2 | 10000 |  |  |  |  |  |  |  |  | StartTool | T0
35 | Cartesian repeat | 8,9,10,11,17,18,24,25,26,27,33,34 | 0 | 0 | 4 | 20 |  |  |  |  |  |  |  | LayerHeight | 0.9
36 |  |  |  |  |  |  |  |  |  |  |  |  |  | Length | 50
37 |  |  |  |  |  |  |  |  |  |  |  |  |  | StartX | 50
38 |  |  |  |  |  |  |  |  |  |  |  |  |  | StartY | 75
39
40
Design ID: | Interlaced_Lines_Alternate_1 | Save to sheet: | MyDesigns |  |  |  |  |  |  |  |  |  |  |  |  |  |  |  |  |  |  |  |  |  |  |  |  |  |  | Save data (DO NOT DELETE): | Save time: 11/16/2021 12:42:00 AM | Design ID: | Interlaced_Lines_Alternate_1 | Save to sheet: | MyDesigns
Feature |  |  |  |  |  |  |  |  |  |  |  |  | Comments
1 | SKIP_Line | Cartesian | X1 | Y1 | Z1 | X2 | Y2 | Z2 | "Print" or "Travel" | NomWidth | NomHeight | E=?;F=?;T=? EvalueOverride;F-SpeedOverride:ToolNumber |  | Settings
2 | SKIP_Custom GCODE | T | 0 |  |  |  |  |  |  |  |  |  | first layer | Zoffset | 0.55 | mm
3 | SKIP_Line | Cartesian | R0 | R0 | R0 | 50 | 50 | 0.55 | Travel |  |  |  |  | FirstLayerExtrusionMultiplier | 0.83 | no units
4 | Line | Cartesian | 40 | 100 | 0 | R15 | R0 | R0 | Print | 3.75 | 2.8 |  |  | FirstLayerNozzleSpeedMultiplier | 0.85 | no units
5 | Line | Cartesian | R0 | R0 | R0 | R0 | R125 | R0 | Print | 3.75 | 2.8 |  |  | ToolChange ID | Default |  | Default | Default | Default | Default | Default | Default | Raise3D_2nozzle | Tool changer | Default | Default | Default | Default | Default
6 | Line | Cartesian | R0 | R0 | R0 | R5 | R0 | R0 | Print | 3.75 | 2.8 |  |  | Start tool (after StartGCODE) | 0
7 | Line | Cartesian | R0 | R0 | R0 | R0 | R-125 | R0 | Print | 3.75 | 2.8
8 | Cartesian repeat | 4-7 | 20 | 0 | 0 | 20 |  |  |  |  |  |  |  | BedTemp | 65 | C | 60 | 60 | 60 | 60 | 60 | 60 | 60 | 60 | 60 | 60 | 60 | 60 | 60
9 | Custom GCODE | M98 P"parkprep.g" |  |  |  |  |  |  |  |  |  |  |  | NozzleFeedratePrinting | 1500 | mm/min
10 | Custom GCODE | T | 1 |  |  |  |  |  |  |  |  |  |  | NozzleFeedrateTravelling | 48000 | mm/min
11 | Custom GCODE | M98 P"prime.g" |  |  |  |  |  |  |  |  |  |  |  | NozzleTemp | 220 | C | 210 | 210 | 210 | 215 | 220 | 210 | 210 | 210 | 210 | 210 | 210 | 210 | 210
12 | SKIP_Line | Cartesian | R0 | R0 | R0 | 55 | 180 | 0.55 | Travel |  |  |  |  | FeedstockFilamentDiameter | 1.75 | mm | 2.85 | 1.75 | 1.75 | 1.75 | 1.75 | 1.75 | 1.75 | 1.75 | 1.75 | 1.75 | 1.75 | 2.85 | 1.75
13 | Line | Cartesian | 45 | 230 | 0.0001 | R0 | R-125 | R0 | Print | 3.75 | 2.8 |  |  | ExtrusionUnits | 33 | mm OR mm3 | mm3 | mm | mm | mm | mm | mm | mm | mm | mm | mm | mm | mm3 | mm
14 | Line | Cartesian | R0 | R0 | R0 | R5 | R0 | R0 | Print | 3.75 | 2.8 |  |  | StartGCODE ID | Toolchanger |  | ULTI2+_Temps&Fan | Ender 3 | CR-10 | PrusaMini | AnycubicMegaS | Raise3D_1nozzle | Raise3D_2nozzle | ToolChanger_T0T2 | Snapmaker 2_A350 | REPRAP X400 | Voxel8 | Ultimaker3 | Artillery Genius
15 | Line | Cartesian | R0 | R0 | R0 | R0 | R125 | R0 | Print | 3.75 | 2.8 |  |  | EndGCODE ID | Toolchanger |  | ULTI2+_1 | Ender 3 | CR-10 | PrusaMini | AnycubicMegaS | Raise3D_1nozzle | Raise3D_2nozzle | ToolChanger_T0T2 | Snapmaker 2_A350 | REPRAP X400 | Voxel8 | Ultimaker3 | Artillery Genius
16 | Line | Cartesian | R0 | R0 | R0 | R15 | R0 | R0 | Print | 3.75 | 2.8 |  |  | Start X (after StartGCODE) | 20 | mm
17 | Cartesian repeat | 13-16 | 20 | 0 | 0 | 20 |  |  |  |  |  |  |  | Start Y (after StartGCODE) | 10 | mm
18 | Retraction | 1.25 | 2100 | 2 | 10000 |  |  |  |  |  |  |  |  | Start Z (after StartGCODE) | 0.3 | mm
19 | SKIP_Line | Cartesian | R0 | R0 | R0 | 55 | 180 |  | Travel |  |  |  |  | FanSpeed | 0
20 | Line | Cartesian | 40 | 100 | R0 | R15 | R0 | R0 | Print | 3.75 | 2.8 |  |  | AutoTravelRetraction? | no | yes/no

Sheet: Demos
Design ID: | Flow mixer | Save to sheet: | Demos |  |  |  |  |  |  |  |  |  |  |  |  |  |  | Save data (DO NOT DELETE): | Save time: 24/07/2020 08:01:19 | Design ID: | Flow mixer | Save to sheet: | Demos
Feature |  |  |  |  |  |  |  |  |  |  |  |  |  | Comments
1 | Circle/arc | 50 | 50 | 0 | 3 | 0 | 360 | CW | 32 | 0.4 | 0.2 |  |  | Outer tube | Settings
2 | Line | Cartesian | R0 | R0 | R0 | R-6 | R0 | R0 | Print | 0.4 | 0.2 |  |  | Line across | Zoffset | 0.2 | mm
3 | Cartesian repeat | 1-2 | 0 | 0 | 0.2 | 150 |  |  |  |  |  |  |  | Repeate for many layers | FirstLayerExtrusionMultiplier | 1 | no units
4 | SKIP_Repeat rule | 3 | 1-2 | 1 | 50 | OffsetPolarIncrement | 50 | 50 | 1.8 | 0 | YES | YES |  | Twist first section | FirstLayerNozzleSpeedMultiplier | 1 | no units
5 | SKIP_Repeat rule | 3 | 1-2 | 51 | 100 | OffsetPolarIncrement | 50 | 50 | -1.8 | 0 | YES | YES |  | Twist second section | ToolChange ID | Default
6 | SKIP_Repeat rule | 3 | 1-2 | 101 | 150 | OffsetPolarIncrement | 50 | 50 | 1.8 | 0 | YES | YES |  | Twist third section | Start tool (after StartGCODE) | 0
7 | SKIP_Postprocess | Y3.51,Y3.101,N1 | OffsetPolar | 50 | 50 | 0 | 0.4 | YES | YES |  |  |  |  | Extend brindge lines
8 | SKIP_Repeat rule | 3 | 1-2 | 1 | 150 | OffsetPolarMaths | 50 | 50 | 0 | (0.5+0.5*COS(((REPval/50)*(2*PI()))-PI()))*2 | 0 | YES | YES | Fluctuate diameter | BedTemp | 60 | C
9 | SKIP_Repeat rule | 3 | 1-2 | 1 | 150 | OffsetLinearMaths | (0.5+0.5*COS(((REPval/150)*(2*PI()))-PI()))*3 | 0 | 0 | YES | YES |  |  | Deviate around components | NozzleFeedratePrinting | 1000 | mm/min
10 | SKIP_Repeat rule | 3 | 1-2 | 151 | 200 | OffsetPolarMaths | 50 | 50 | 0 | ((sin(2*Aval-(pi()/2)))*0.08+0.02)*REPval | 0 | YES | YES |  | NozzleFeedrateTravelling | 9000 | mm/min
11 | SKIP_Repeat rule | 3 | 1-2 | 151 | 200 | OffsetLinearMaths | 0 | 0 | ((xval-50)/20)*(0.2*REPval) | YES | YES |  |  |  | NozzleTemp | 210 | C
12 |  |  |  |  |  |  |  |  |  |  |  |  |  |  | FeedstockFilamentDiameter | 2.85 | mm
13 |  |  |  |  |  |  |  |  |  |  |  |  |  |  | ExtrusionUnits | mm3 | mm OR mm3
14 |  |  |  |  |  |  |  |  |  |  |  |  |  |  | StartGCODE ID | ULTI2+_Temps&Fan
15 |  |  |  |  |  |  |  |  |  |  |  |  |  |  | EndGCODE ID | ULTI2+_1
 |  |  |  |  |  |  |  |  |  |  |  |  |  |  | Start X (after StartGCODE) | 20 | mm
 |  |  |  |  |  |  |  |  |  |  |  |  |  |  | Start Y (after StartGCODE) | 10 | mm
 |  |  |  |  |  |  |  |  |  |  |  |  |  |  | Start Z (after StartGCODE) | 0.3 | mm
 |  |  |  |  |  |  |  |  |  |  |  |  |  |  | FanSpeed | 0
 |  |  |  |  |  |  |  |  |  |  |  |  |  |  | AutoTravelRetraction? | no | yes/no
 |  |  |  |  |  |  |  |  |  |  |  |  |  |  | - Threshold distance | 5 | mm
 |  |  |  |  |  |  |  |  |  |  |  |  |  |  | - Retraction (E-value) | 7 | mm OR mm3
 |  |  |  |  |  |  |  |  |  |  |  |  |  |  | - Retraction speed (F-value) | 2500 | mm/min
 |  |  |  |  |  |  |  |  |  |  |  |  |  |  | - Unretraction (E-value) | -7 | mm OR mm3
 |  |  |  |  |  |  |  |  |  |  |  |  |  |  | - Unretraction speed (F-value) | 2500 | mm/min
 |  |  |  |  |  |  |  |  |  |  |  |  |  |  | - Z-hop | 0.2 | mm
 |  |  |  |  |  |  |  |  |  |  |  |  |  |  | - Z-hop speed (F-value) | 7500 | mm/min
 |  |  |  |  |  |  |  |  |  |  |  |  |  |  | Parameter name | Parameter value | Units
Design ID: | String Calibration | Save to sheet: | Demos |  |  |  |  |  |  |  |  |  |  |  |  |  |  | Save data (DO NOT DELETE): | Save time: 27/07/2020 09:05:06 | Design ID: | String Calibration | Save to sheet: | Demos
Feature |  |  |  |  |  |  |  |  |  |  |  |  |  | Comments
1 | Rectangle | 50 | 50 | R50 | R20 | 0 | CW | 0.4 | 0.2 |  |  |  |  | Rectangle base | Settings
2 | Line | Cartesian | R0 | R0 | R0 | R5 | R0 | R0 | Travel |  |  |  |  | Move to start (5mm right) | Zoffset | 0.2 | mm
3 | Custom GCODE | G1 E | 1 | F | 2000 |  |  |  |  |  |  |  |  |  | FirstLayerExtrusionMultiplier | 1 | no units
4 | Line | Cartesian | R0 | R0 | R0 | R0 | R0 | R0.3 | Travel | 0 | 0 | F=500 |  | Move up | FirstLayerNozzleSpeedMultiplier | 1 | no units
5 | Line | Cartesian | R0 | R0 | R0 | R0 | R20 | R0 | Travel | 0 | 0 | F=6000 |  | Move across | ToolChange ID | Default
6 | Line | Cartesian | R0 | R0 | R0 | R0 | R0 | R-0.3 | Travel | 0 | 0 | F=500 |  | Move down | Start tool (after StartGCODE) | 0
7 | Line | Cartesian | R0 | R0 | R0 | R2 | R0 | R0 | Travel | 0 | 0 | F=500 |  | Move sideways to begin next string
8 | Custom GCODE | G1 E | 1 | F | 2000 |  |  |  |  |  |  |  |  |  | BedTemp | 60 | C
9 | Line | Cartesian | R0 | R0 | R0 | R0 | R0 | R0.3 | Travel | 0 | 0 | F=500 |  | Move up | NozzleFeedratePrinting | 1000 | mm/min
10 | Line | Cartesian | R0 | R0 | R0 | R0 | R-20 | R0 | Travel | 0 | 0 | F=6000 |  | Move across | NozzleFeedrateTravelling | 9000 | mm/min
11 | Line | Cartesian | R0 | R0 | R0 | R0 | R0 | R-0.3 | Travel | 0 | 0 | F=500 |  | Move down | NozzleTemp | 210 | C
12 | Line | Cartesian | R0 | R0 | R0 | R2 | R0 | R0 | Travel | 0 | 0 | F=500 |  | Move sideways to begin next string | FeedstockFilamentDiameter | 2.85 | mm
13 | Cartesian repeat | 3-12 | 4 | 0 | 0 | 9 |  |  |  |  |  |  |  | Repeat strings | ExtrusionUnits | mm3 | mm OR mm3
14 | Repeat rule | 13 | 3,8 | 1 | 9 | GenericParameterIncrement | 3 | 0.5 |  |  |  |  |  | Vary amount of extrusion | StartGCODE ID | ULTI2+_Temps&Fan
15 |  |  |  |  |  |  |  |  |  |  |  |  |  |  | EndGCODE ID | ULTI2+_1
 |  |  |  |  |  |  |  |  |  |  |  |  |  |  | Start X (after StartGCODE) | 20 | mm
 |  |  |  |  |  |  |  |  |  |  |  |  |  |  | Start Y (after StartGCODE) | 10 | mm
 |  |  |  |  |  |  |  |  |  |  |  |  |  |  | Start Z (after StartGCODE) | 0.3 | mm
 |  |  |  |  |  |  |  |  |  |  |  |  |  |  | FanSpeed | 0
 |  |  |  |  |  |  |  |  |  |  |  |  |  |  | AutoTravelRetraction? | no | yes/no
 |  |  |  |  |  |  |  |  |  |  |  |  |  |  | - Threshold distance | 5 | mm
 |  |  |  |  |  |  |  |  |  |  |  |  |  |  | - Retraction (E-value) | 7 | mm OR mm3
 |  |  |  |  |  |  |  |  |  |  |  |  |  |  | - Retraction speed (F-value) | 2500 | mm/min
 |  |  |  |  |  |  |  |  |  |  |  |  |  |  | - Unretraction (E-value) | -7 | mm OR mm3
 |  |  |  |  |  |  |  |  |  |  |  |  |  |  | - Unretraction speed (F-value) | 2500 | mm/min
 |  |  |  |  |  |  |  |  |  |  |  |  |  |  | - Z-hop | 0.2 | mm
 |  |  |  |  |  |  |  |  |  |  |  |  |  |  | - Z-hop speed (F-value) | 7500 | mm/min
 |  |  |  |  |  |  |  |  |  |  |  |  |  |  | Parameter name | Parameter value | Units
Design ID: | Box | Save to sheet: | Demos |  |  |  |  |  |  |  |  |  |  |  |  |  |  | Save data (DO NOT DELETE): | Save time: 27/07/2020 09:40:25 | Design ID: | Box | Save to sheet: | Demos
Feature |  |  |  |  |  |  |  |  |  |  |  |  |  | Comments
1 | Line | Cartesian | 50 | 50 | 0 | R50 | R0 | R0 | Print | 0.4 | 0.2 |  |  |  | Settings
2 | Line | Cartesian | R0 | R0 | R0 | R0 | R50 | R0 | Print | 0.4 | 0.2 |  |  |  | Zoffset | 0.2 | mm
3 | Line | Cartesian | R0 | R0 | R0 | R-50 | R0 | R0 | Print | 0.4 | 0.2 |  |  |  | FirstLayerExtrusionMultiplier | 1 | no units
4 | Line | Cartesian | R0 | R0 | R0 | R0 | R-50 | R0 | Print | 0.4 | 0.2 |  |  |  | FirstLayerNozzleSpeedMultiplier | 1 | no units
5 | Cartesian repeat | 1-4 | 0 | 0 | 0.2 | 250 |  |  |  |  |  |  |  |  | ToolChange ID | Default
6 |  |  |  |  |  |  |  |  |  |  |  |  |  |  | Start tool (after StartGCODE) | 0
7
8 |  |  |  |  |  |  |  |  |  |  |  |  |  |  | BedTemp | 60 | C
9 |  |  |  |  |  |  |  |  |  |  |  |  |  |  | NozzleFeedratePrinting | 1000 | mm/min
10 |  |  |  |  |  |  |  |  |  |  |  |  |  |  | NozzleFeedrateTravelling | 9000 | mm/min
11 |  |  |  |  |  |  |  |  |  |  |  |  |  |  | NozzleTemp | 210 | C
12 |  |  |  |  |  |  |  |  |  |  |  |  |  |  | FeedstockFilamentDiameter | 2.85 | mm
13 |  |  |  |  |  |  |  |  |  |  |  |  |  |  | ExtrusionUnits | mm3 | mm OR mm3
14 |  |  |  |  |  |  |  |  |  |  |  |  |  |  | StartGCODE ID | ULTI2+_Temps&Fan
15 |  |  |  |  |  |  |  |  |  |  |  |  |  |  | EndGCODE ID | ULTI2+_1
 |  |  |  |  |  |  |  |  |  |  |  |  |  |  | Start X (after StartGCODE) | 20 | mm
 |  |  |  |  |  |  |  |  |  |  |  |  |  |  | Start Y (after StartGCODE) | 10 | mm
 |  |  |  |  |  |  |  |  |  |  |  |  |  |  | Start Z (after StartGCODE) | 0.3 | mm
 |  |  |  |  |  |  |  |  |  |  |  |  |  |  | FanSpeed | 0
 |  |  |  |  |  |  |  |  |  |  |  |  |  |  | AutoTravelRetraction? | no | yes/no
 |  |  |  |  |  |  |  |  |  |  |  |  |  |  | - Threshold distance | 5 | mm
 |  |  |  |  |  |  |  |  |  |  |  |  |  |  | - Retraction (E-value) | 7 | mm OR mm3
 |  |  |  |  |  |  |  |  |  |  |  |  |  |  | - Retraction speed (F-value) | 2500 | mm/min
 |  |  |  |  |  |  |  |  |  |  |  |  |  |  | - Unretraction (E-value) | -7 | mm OR mm3
 |  |  |  |  |  |  |  |  |  |  |  |  |  |  | - Unretraction speed (F-value) | 2500 | mm/min
 |  |  |  |  |  |  |  |  |  |  |  |  |  |  | - Z-hop | 0.2 | mm
 |  |  |  |  |  |  |  |  |  |  |  |  |  |  | - Z-hop speed (F-value) | 7500 | mm/min
 |  |  |  |  |  |  |  |  |  |  |  |  |  |  | Parameter name | Parameter value | Units
Design ID: | Tutorial_RepeatRule | Save to sheet: | Demos |  |  |  |  |  |  |  |  |  |  |  |  |  |  | Save data (DO NOT DELETE): | Save time: 22/10/2020 08:40:14 | Design ID: | Tutorial_RepeatRule | Save to sheet: | Demos
Feature |  |  |  |  |  |  |  |  |  |  |  |  |  | Comments
1 | Line | Cartesian | 50 | 50 | 0 | R20 | R0 | R0 | Print | 0.5 | 0.2 |  |  |  | Settings
2 | Line | Cartesian | R0 | R0 | R0 | R0 | R20 | R0 | Print | 0.5 | 0.2 |  |  |  | Zoffset | 0.2 | mm
3 | Line | Cartesian | R0 | R0 | R0 | R-20 | R0 | R0 | Print | 0.5 | 0.2 |  |  |  | FirstLayerExtrusionMultiplier | 1 | no units
4 | Line | Cartesian | R0 | R0 | R0 | R0 | R-20 | R0 | Print | 0.5 | 0.2 |  |  |  | FirstLayerNozzleSpeedMultiplier | 1 | no units
5 | Cartesian repeat | 1-4 | 0 | 0 | 0.2 | 100 |  |  |  |  |  |  |  |  | ToolChange ID | Default
6 | Repeat rule | 5 | 2 | 50 | 100 | OffsetLinearIncrement | 0.2 | 0 | 0 | YES | YES |  |  |  | Start tool (after StartGCODE) | 0
7 | Repeat rule | 5 | 1 | 50 | 100 | OffsetLinearIncrement | 0.2 | 0 | 0 | NO | YES
8 | Repeat rule | 5 | 3 | 50 | 100 | OffsetLinearIncrement | 0.2 | 0 | 0 | YES | NO |  |  |  | BedTemp | 60 | C
9 | SKIP_Repeat rule | 5 | 2 | 50 | 100 | OffsetLinearIncrementGraded | 0.005 | 0 | 0 | YES | YES |  |  |  | NozzleFeedratePrinting | 1000 | mm/min
10 | SKIP_Repeat rule | 5 | 1 | 50 | 100 | OffsetLinearIncrementGraded | 0.005 | 0 | 0 | NO | YES |  |  |  | NozzleFeedrateTravelling | 9000 | mm/min
11 | SKIP_Repeat rule | 5 | 3 | 50 | 100 | OffsetLinearIncrementGraded | 0.005 | 0 | 0 | YES | NO |  |  |  | NozzleTemp | 210 | C
12 | SKIP_Repeat rule | 5 | 1-4 | 50 | 100 | OffsetPolar | 60 | 60 | 45 | 0 | YES | YES |  |  | FeedstockFilamentDiameter | 2.85 | mm
13 | SKIP_Repeat rule | 5 | 1-4 | 50 | 100 | OffsetPolarIncrement | 50 | 50 | 0 | 0.2 | YES | YES |  |  | ExtrusionUnits | mm3 | mm OR mm3
14 | SKIP_Repeat rule | 5 | 1-4 | 50 | 100 | NomWidth | 1 |  | Value of width for each repeat this rule applies to |  |  |  |  |  | StartGCODE ID | ULTI2+_Temps&Fan
15 | SKIP_Repeat rule | 5 | 1-4 | 50 | 100 | NomWidthIncrement | 0.01 |  | How much to change the width by (absolute) for each repeat this rule applies to (cumulative) |  |  |  |  |  | EndGCODE ID | ULTI2+_1
16 | SKIP_Repeat rule | 5 | 1-4 | 50 | 100 | Fspeed | VALUE |  | Value of speed for each repeat this rule applies to |  |  |  |  |  | Start X (after StartGCODE) | 20 | mm
17 | SKIP_Repeat rule | 5 | 1-4 | 50 | 100 | FspeedIncrement | 10 |  | How much to change the wpeed by (absolute) for each repeat this rule applies to (cumulative) |  |  |  |  |  | Start Y (after StartGCODE) | 10 | mm
18 |  |  |  |  |  |  |  |  |  |  |  |  |  |  | Start Z (after StartGCODE) | 0.3 | mm
19 |  |  |  |  |  |  |  |  |  |  |  |  |  |  | FanSpeed | 0
 |  |  |  |  |  |  |  |  |  |  |  |  |  |  | AutoTravelRetraction? | no | yes/no
 |  |  |  |  |  |  |  |  |  |  |  |  |  |  | - Threshold distance | 5 | mm
 |  |  |  |  |  |  |  |  |  |  |  |  |  |  | - Retraction (E-value) | 7 | mm OR mm3
 |  |  |  |  |  |  |  |  |  |  |  |  |  |  | - Retraction speed (F-value) | 2500 | mm/min
 |  |  |  |  |  |  |  |  |  |  |  |  |  |  | - Unretraction (E-value) | -7 | mm OR mm3
 |  |  |  |  |  |  |  |  |  |  |  |  |  |  | - Unretraction speed (F-value) | 2500 | mm/min
 |  |  |  |  |  |  |  |  |  |  |  |  |  |  | - Z-hop | 0.2 | mm
 |  |  |  |  |  |  |  |  |  |  |  |  |  |  | - Z-hop speed (F-value) | 7500 | mm/min
 |  |  |  |  |  |  |  |  |  |  |  |  |  |  | Parameter name | Parameter value | Units
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

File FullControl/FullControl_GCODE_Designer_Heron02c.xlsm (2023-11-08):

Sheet: Main Sheet
 |  |  |  |  |  |  |  | ;GCODE generated with FullControl GCODE Designer software - contact Andy Gleadall (a.gleadall@lboro.ac.uk) for more information
 |  |  |  |  |  |  |  |  |  |  |  |  |  |  | Recycle bin designs: | 1
Design ID: | Interlaced_Lines_Alternate_1 | Save to sheet: | MyDesigns
Feature |  |  |  |  |  |  |  |  |  |  |  |  | Comments
1 | SKIP_Line | Cartesian | X1 | Y1 | Z1 | X2 | Y2 | Z2 | "Print" or "Travel" | NomWidth | NomHeight | E=?;F=?;T=? EvalueOverride;F-SpeedOverride:ToolNumber |  | Settings
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

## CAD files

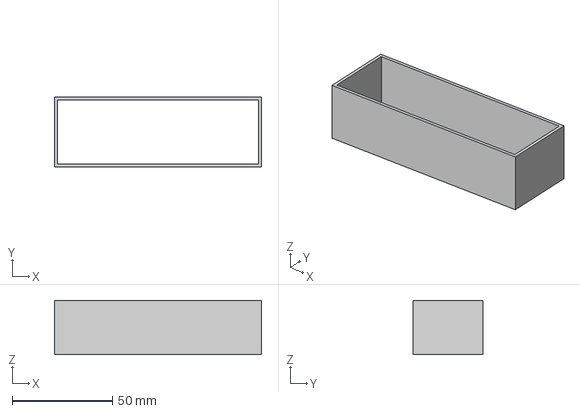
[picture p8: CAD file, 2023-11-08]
Parts/Cast_Mold/Cast_Mold_1.3mf
103.0 x 35.0 x 27.0 mm

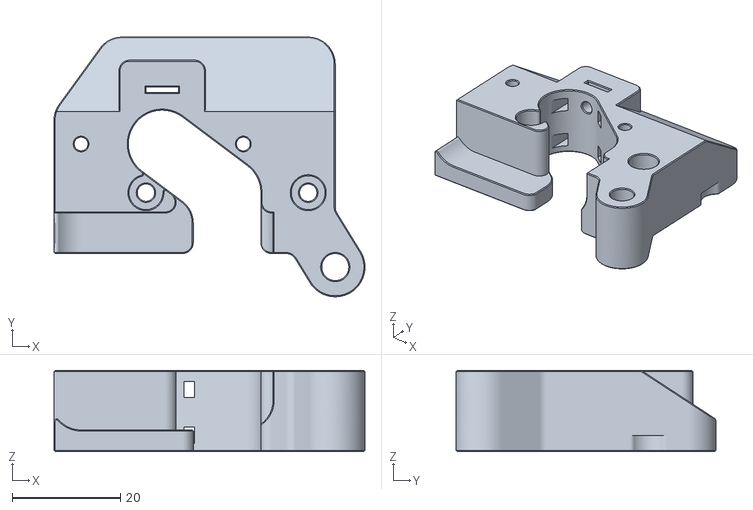
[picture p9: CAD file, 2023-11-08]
Parts/Hemera Tool/TC-DOCK-V6-DOCK-ADAPTER.stl
57.5 x 48.0 x 15.0

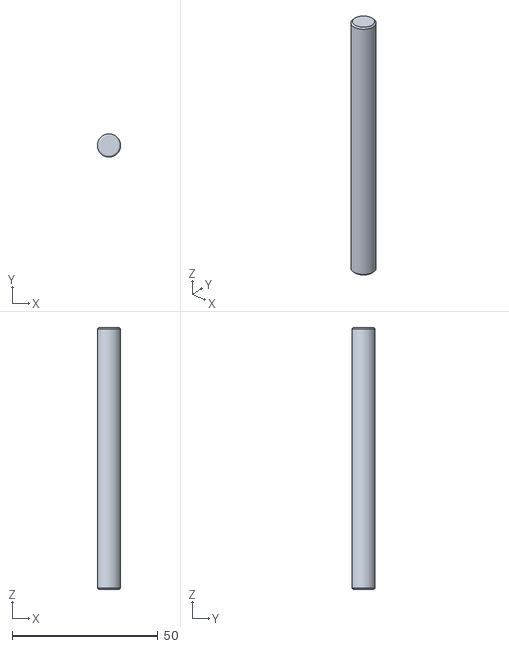
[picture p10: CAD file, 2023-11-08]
Parts/Misc/Spool Bar.stl
8.00 x 7.99 x 90.0

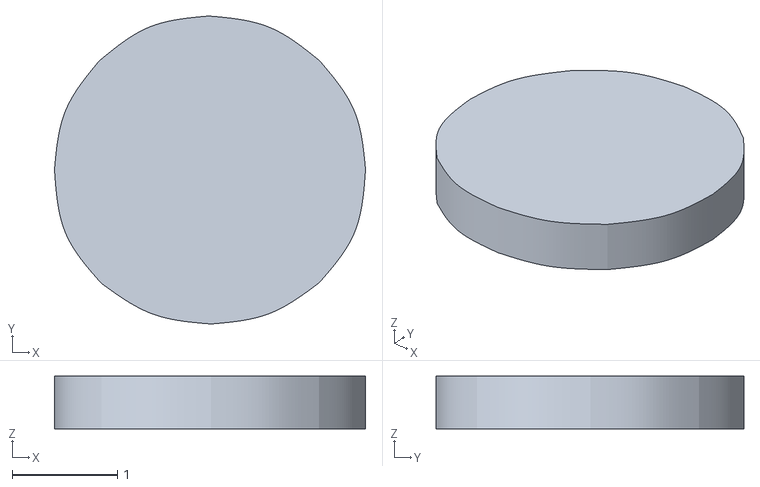
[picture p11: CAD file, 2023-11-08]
Parts/Motion System/Tool-Changer Cover Dot.stl
2.95 x 2.92 x 0.5

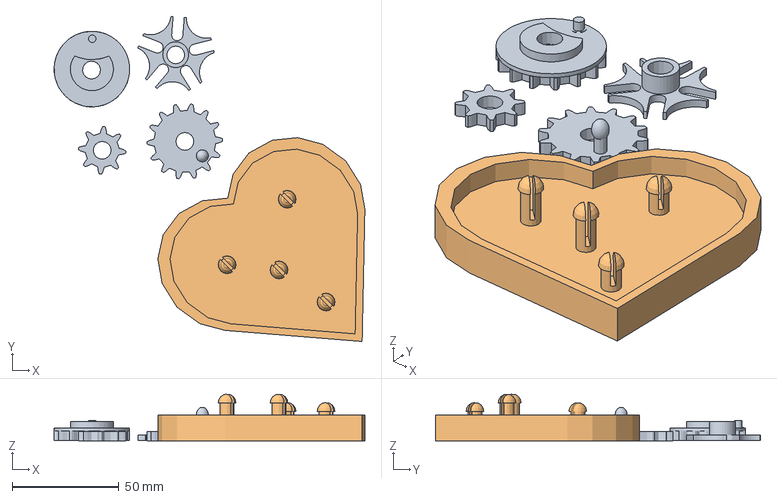
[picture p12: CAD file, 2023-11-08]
Parts/Ooze_Bucket/Plexi_Mount_Extended.3mf
145.4 x 152.1 x 21.8 mm
gears.stl
heart_base.stl

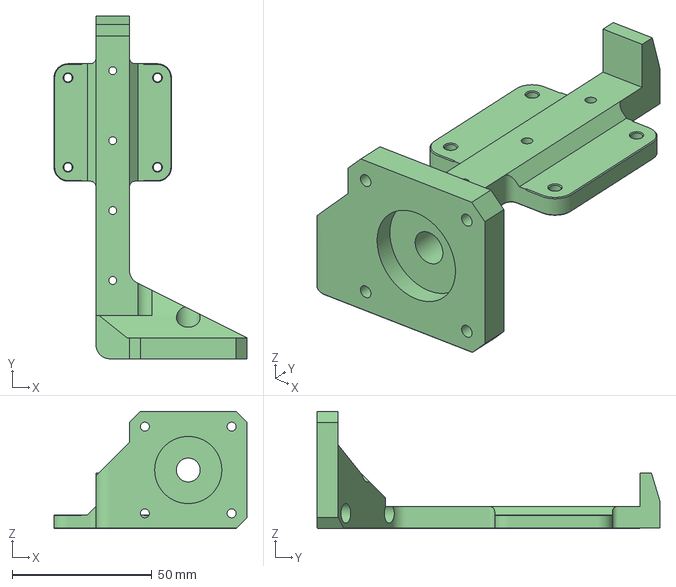
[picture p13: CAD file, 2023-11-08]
Parts/Pebble_Wiper/Adjustable_Brush_Frame_3.3mf
69.0 x 122.5 x 42.0 mm

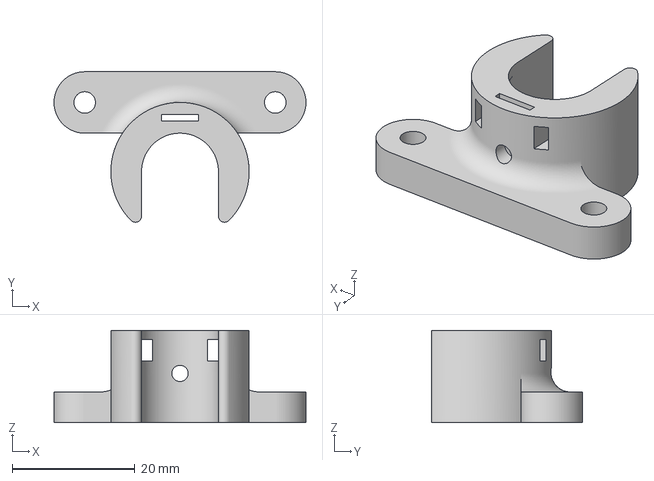
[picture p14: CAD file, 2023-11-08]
Parts/SDS_Mount/Cable_Support/SDS_Cable_Support.3mf
41.0 x 24.5 x 15.0 mm

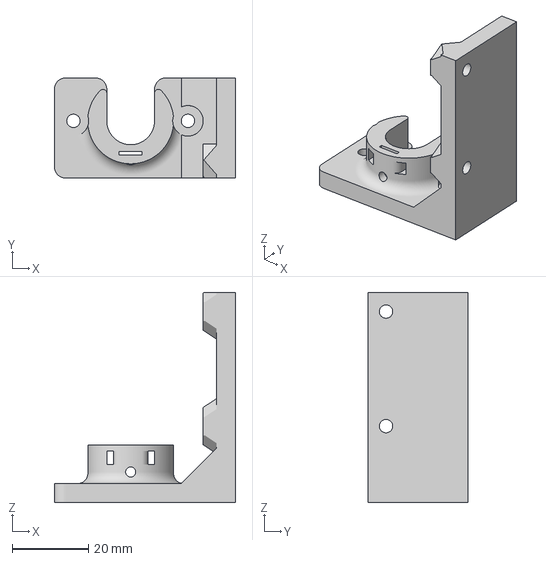
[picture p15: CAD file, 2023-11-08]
Parts/SDS_Mount/Dock_Adapter/SDS_Dock_Adapter.3mf
47.5 x 26.2 x 55.0 mm

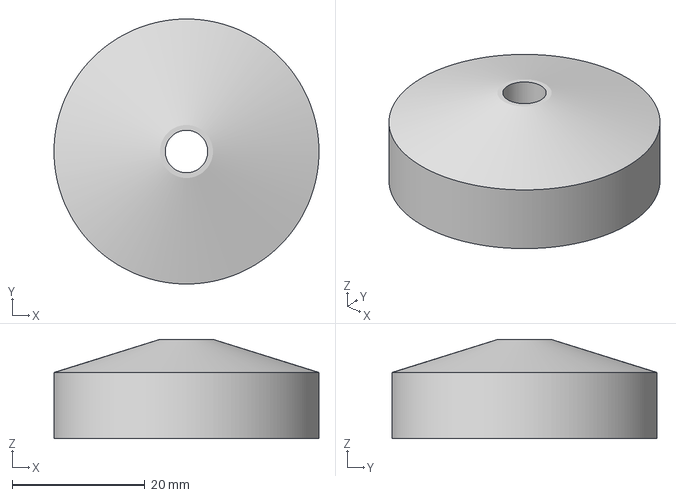
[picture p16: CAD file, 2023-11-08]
Parts/SDS_Mount/Luer_Adapter/150cc_Syringe_Luer_Adapter_1.3mf
40.0 x 40.0 x 15.0 mm

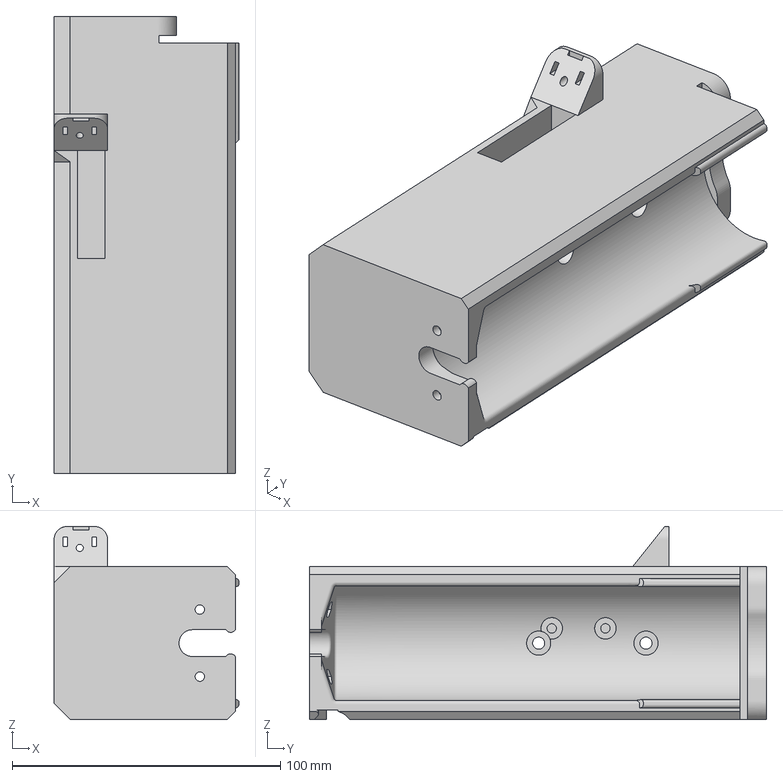
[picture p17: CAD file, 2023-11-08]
Parts/SDS_Mount/SDS_ToolChanger_Mount_3.3mf
68.9 x 170.5 x 72.0 mm

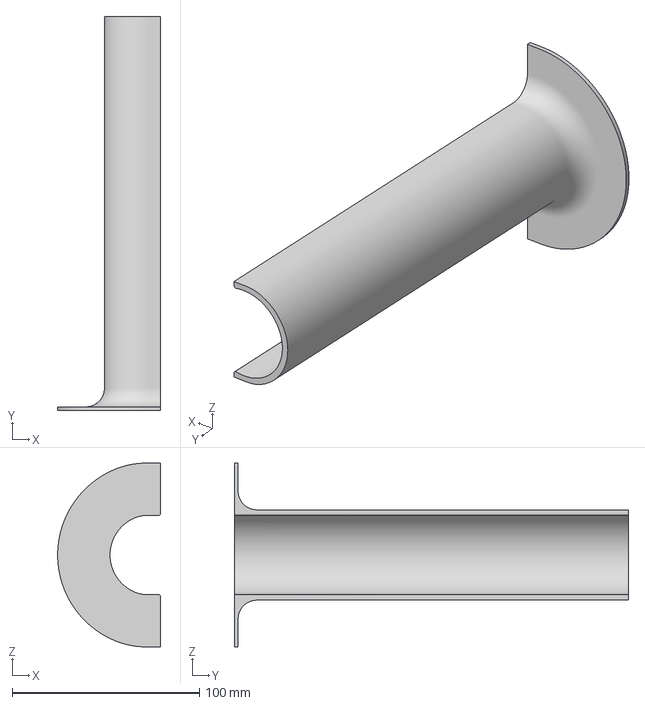
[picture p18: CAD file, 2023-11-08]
Parts/SDS_Vibration_Mount/SDS_Vibration_Mount.3mf
54.8 x 210.5 x 98.2 mm

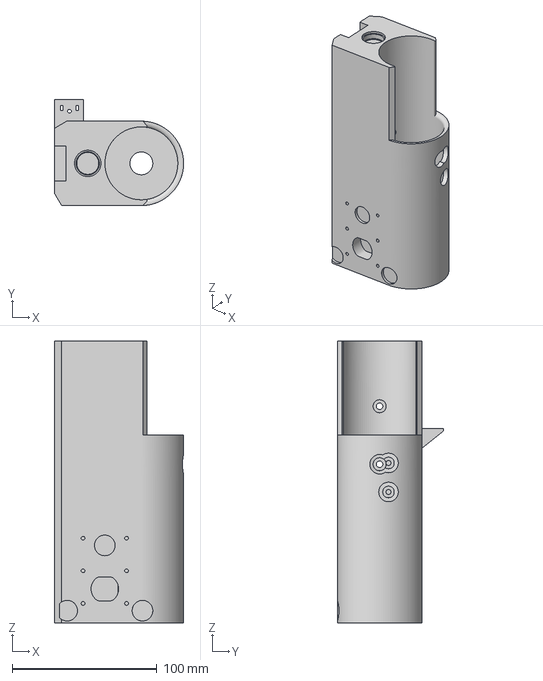
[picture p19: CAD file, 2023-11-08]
Parts/Silicone_Extruder/Silicone_Extruder_ToolChanger_Mount_2.3mf
89.1 x 73.2 x 194.5 mm

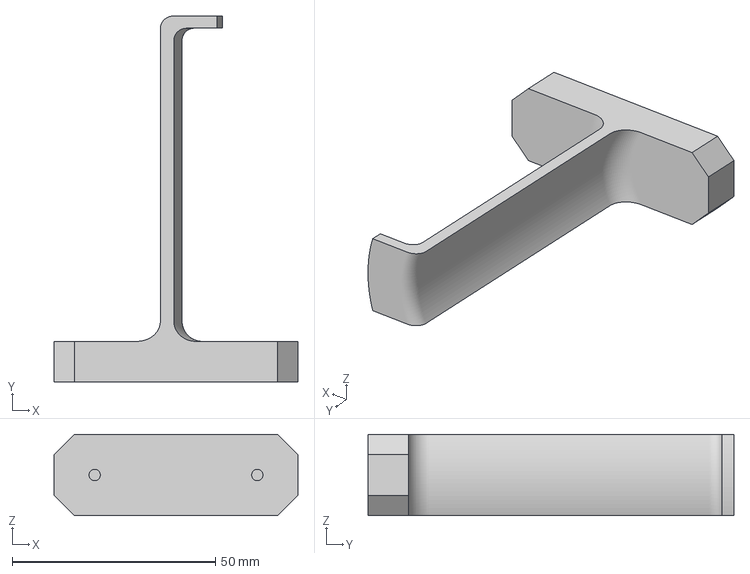
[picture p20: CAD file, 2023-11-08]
Parts/SpoolHolder/ToolChanger_SpoolHolder.3mf
60.0 x 90.0 x 20.0 mm

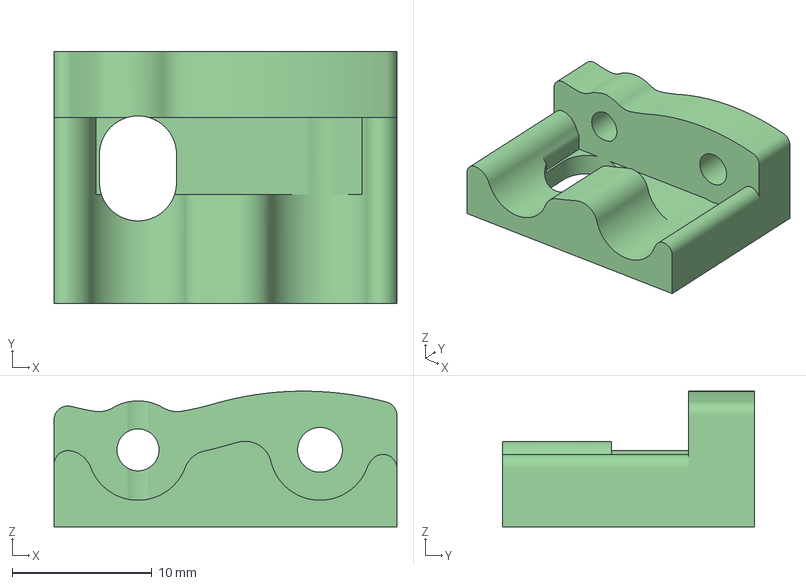
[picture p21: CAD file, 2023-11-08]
Parts/Z_Stop_Saver/Z_Endstop_Saver.3mf
24.5 x 18.0 x 9.69 mm

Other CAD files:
Parts/Cast_Mold/Cast_Mold.3mf
Parts/Hemera Tool/Hemera_PCF_Duct_-_V6.stl
Parts/Misc/Cable Blank.stl
Parts/Motion System/Tool-Changer Cover Triangle.stl
Parts/Hemera Tool/Hemera_PCF_Bracket.stl
Parts/Hemera Tool/Hemera_PCF_Duct_-_Volcano.stl
Parts/Hemera Tool/TC-HEMERA-PLATE-ADAPTER.stl
Parts/Hemera Tool/TC-V6-DOCK-BRACKET-HEMERA-ADAPTER.stl
Parts/Hemera Tool/TC-V6-HEMERA-DOCK-BRACE-V2.stl
Parts/Hemera Tool/TC-V6-HEMERA-DOCK-BRACE.stl
Parts/Hemera Tool/V6_Cable_Support.stl
Parts/Hemera Tool/V6_Receiver_Top.stl
Parts/Misc/Filament Pick-Up.stl
Parts/Misc/Hemera Bowden Bracket.stl
Parts/Misc/IEC Bracket.stl
Parts/Misc/IEC Socket.stl
Parts/Misc/Motor Cable Cover.stl
Parts/Misc/PSU Duct.stl
Parts/Misc/Spool Bar_Split.stl
Parts/Misc/Spool Bar_Split_1.3mf
Parts/Misc/Spool Carrier.stl
Parts/Misc/Wiper.stl
Parts/Motion System/Hemera Bowden Bracket_x2.stl
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

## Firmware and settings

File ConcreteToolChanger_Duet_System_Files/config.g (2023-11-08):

; Configuration file for Duet WiFi / Ethernet running RRF3 on E3D Tool Changer
; executed by the firmware on start-up

; General preferences
M111 S0 						; Debugging off
G21 							; Work in millimetres
G90 							; Send absolute coordinates...
M83 							; ...but relative extruder moves
M555 P2 						; Set firmware compatibility to look like Marlin
M667 S1 						; Select CoreXY mode	

; Network
M550 P"ConcreteToolChanger"     ; Set machine name
M551 P"concretetoolchanger"		; set DWC access password
;M587 S"ssid" P"password"		; WiFi Settings
;M552 S1 P"ssid"				; Enable WiFi Networking
M552 S1 P192.168.2.1			; Enable Networking with static IP
M586 P0 S1 						; Enable HTTP
M586 P1 S0 						; Disable FTP
M586 P2 S0 						; Disable Telnet

; Drive direction
M569 P0 S0 						; Drive 0 X
M569 P1 S0 						; Drive 1 Y
M569 P2 S1 						; Drive 2 Z
M569 P3 S1 						; Drive 3 E0
M569 P4 S1 						; Drive 4 E1
M569 P5 S1 						; Drive 5 E2
M569 P6 S1 						; Drive 6 E3
M569 P7 S0 						; Drive 7 COUPLER
M569 P8 S1 						; Drive 8 WIPER
M569 P9 S0 						; Drive 9 UNUSED

M584 X0 Y1 Z2 C7 W8 E3:4:5:6 								; Apply custom drive mapping
M208 X-35:328.5 Y-49:243 Z0:300 C-45:360 W-65:58	 				; Set axis maxima & minima
M92 X100 Y100 Z800 C91.022 W400 E407:407:15920.4:15920.4 				; Set steps per mm assuming x16 microstepping
M350 E16:16:16:16 I1 									; Configure microstepping with interpolation
M350 C16 W16 I10											; Configure microstepping without interpolation
M350 X16 Y16 Z16 I1										; Configure microstepping with interpolation
M566 X400 Y400 Z8 C2 W6 E2:2:2:2							; Set maximum instantaneous speed changes (mm/min)
M203 X35000 Y35000 Z1200 C20000 W10000 E5000:5000:5000:5000	; Set maximum speeds (mm/min)
M203 I10 													; set minimum speeds (mm/min)
M201 X6000 Y6000 Z400 C500 W500 E2500:2500:2500:2500			; Set accelerations (mm/s^2)
M906 X1800 Y1800 Z1330 W1000 I30   						; Idle motion motors to 30%
M906 E1000:1000:1000:1000 C500 I10     						; Idle extruder motors to 10%

; Endstops
M574 X1 Y1 W1 S3 					; Set X / Y endstop stall detection
M574 C0 Z0 						; No C Z W endstop

; Z probe
M558 P8 C"zstop" H3 F360 I0 T20000 	; Set Z probe type to switch, the axes for which it is used and the dive height + speeds
G31 P200 X0 Y0 Z0	 				; Set Z probe trigger value, offset and trigger height
M557 X10:290 Y20:180 S40 			; Define mesh grid

;Stall Detection
M915 X Y S3 F0 H400 R4700				; X / Y Axes

; Heaters
M308 S0 P"bedtemp" Y"thermistor" A"Bed" T100000 B4138 C0 		; Set thermistor 
M950 H0 C"bedheat" T0											; Bed heater
M143 H0 S225 													; Set temperature limit for heater 0 to 225C
M140 H0															; Bed heater is heater 0

M308 S1 P"e0temp" Y"thermistor" A"T0" T100000 B4725 C7.06e-8 	; Set thermistor
M950 H1 C"e0heat" T1											; Extruder 0 heater
M143 H1 S305 													; Set temperature limit for heater 1 to 300C

M308 S2 P"e1temp" Y"thermistor" A"T1" T100000 B4725 C7.06e-8 	; Set thermistor
M950 H2 C"e1heat" T2											; Extruder 1 heater
M143 H2 S305 													; Set temperature limit for heater 2 to 300C

M308 S3 P"e2temp" Y"thermistor" A"T2" T100000 B4725 C7.06e-8 	; Set thermistor
;M950 H3 C"duex.e2heat" T3										; Extruder 2 heater
;M143 H3 S305 													; Set temperature limit for heater 3 to 300C

M308 S4 P"e3temp" Y"thermistor" A"T3" T100000 B4725 C7.06e-8 	; Set thermistor
;M950 H4 C"duex.e3heat" T4										; Extruder 3 heater
;M143 H4 S305 													; Set temperature limit for heater 4 to 300C


; Tools
M563 P0 S"T0" D0 H1 F2 					; Define tool 0
G10 P0 X0 Y0 Z0 						; Reset tool 0 axis offsets
G10 P0 R0 S0 							; Reset initial tool 0 active and standby temperatures to 0C

M563 P1 S"T1" D1 H2 F4 					; Define tool 1
G10 P1 X0 Y0 Z0 						; Reset tool 1 axis offsets
G10 P1 R0 S0 							; Reset initial tool 1 active and standby temperatures to 0C

M563 P2 S"T2" D2 ;H3 F6 					; Define tool 2
G10 P2 X0 Y0 Z0 						; Reset tool 2 axis offsets
;G10 P2 R0 S0 							; Reset initial tool 2 active and standby temperatures to 0C

M563 P3 S"T3" D3 ;H4 F8 					; Define tool 3
G10 P3 X0 Y0 Z0 						; Reset tool 3 axis offsets
;G10 P3 R0 S0 							; Reset initial tool 3 active and standby temperatures to 0C

; Fans
M950 F1 C"fan1"
M950 F2 C"fan2"
M950 F3 C"duex.fan3"
M950 F4 C"duex.fan4"
M950 F5 C"duex.fan5"
M950 F6 C"duex.fan6"
M950 F7 C"duex.fan7"
M950 F8 C"duex.fan8"

M106 P1 S255 H1 T70				; T0 HE
M106 P2 S0						; T0 PCF
M106 P3 S255 H2 T70 			; T1 HE
M106 P4 S0						; T1 PCF 
;M106 P5 S255 H3 T70 			; T2 HE 
;M106 P6 S0 						; T2 PCF
;M106 P7 S255 H4 T70				; T3 HE
;M106 P8 S0						; T3 PCF

M593 F42.2						; cancel ringing at 42.2Hz (https://forum.e3d-online.com/threads/accelerometer-and-resonance-measurements-of-the-motion-system.3445/)
;M376 H15						; bed compensation taper

;tool offsets
; !ESTIMATED! offsets for:
; V6-tool: X-9 Y39 Z-5
; Volcano-tool: X-9 Y39 Z-13.5
; Hemera-tool: X20 Y43.5 Z-6

; TOOL OFFSETS
G10 P0 X20 Y43.5 Z-14.6					; T0
G10 P1 X20.38 Y43.9 Z-14.35					; T1
; Stock Nozzle: Z-26
; dark green luer: Z-26.68
; light green luer: Z-34.63
G10 P2 X28 Y46.4 Z-26.25				; T2
; silicone tube, smallest opening: -58.75
;G10 P3 X21.7 Y52 Z-54.1				; T3
G10 P3 X21.7 Y48 Z-52.5			; T3


;M572 D0 S0.2 						; pressure advance T0
;M572 D1 S0.2 						; pressure advance T1
;M572 D2 S0.2 						; pressure advance T2
;M572 D3 S0.2 						; pressure advance T3

M950 P0 C"duex.gp2" Q333			; wiper servo
M42 P0 S0.24						; set to default position

M307 H1 B0 R1.667 C245.2:175.7 D6.27 S1.00 V24.2	; PID tuning H1
M307 H2 B0 R1.634 C220.0:172.6 D5.73 S1.00 V24.2	; PID tuning H1

M575 P1 S1 B57600				; Enable LCD
G29 S2							    ; disable mesh
T-1								      ; deselect tools

M98 P"set_variables.g"			; create printing variables

M501                    ; load config-override.g
